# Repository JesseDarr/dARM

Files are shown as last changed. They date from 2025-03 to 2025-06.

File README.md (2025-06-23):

# dARM (dynamic Arm for Robotic Mischief)
dARM is a 3d printed 6 DOF robotic arm. Initially, I wanted to build a 3d printed arm as a test of my new `Bambu X1C`. I found most existing projects used stepper motors.  I wanted a better power density.

https://github.com/user-attachments/assets/527a8380-1c22-4416-9524-2030928b34a5

So the dARM journey began. The goal was to design a cheap, powerful, robust, modular, and easily maintained arm from scratch using `ODrive S1` BLDC controllers.  It stands `.975 meters` tall and can easily hold `5 lbs` in the horizontal position.

https://github.com/user-attachments/assets/cb6a208b-52ac-4bd4-9993-00c22c082488

After iterating through various designs, modularity and maintenance became top priorities.  If any individual component fails, its modular section can be removed from the larger arm for easy replacement.

## Table of Contents
1. [Versions](#versions)
2. [Inspirations](#inspirations)
   - [James Burton](#james-burton)
   - [Skyentific](#skyentific)
   - [OpenQDD](#openqdd)
   - [SSG48 Gripper](#ssg48-gripper)
   - [Gary McLendon](#gary-mclendon)
3. [Control](#control)
   - [Pi](#pi)
     - [Enable CAN Communication](#enable-can-communication)
     - [CAN Service](#can-service)
     - [Clone git repo](#clone-git-repo)
     - [Game Controllers](#game-controllers)
   - [CAN Wiring](#can-wiring)
4. [Power](#power)
   - [Power Box](#power-box)
   - [Power Wiring](#power-wiring)
5. [Mechanical](#mechanical)
   - [Primary Actuators](#primary-actuators)
   - [Forearm](#forearm)
   - [Gripper](#gripper)
   - [Pillars](#pillars)
6. [Assembly](#assembly)
   - [Sanding](#sanding)
   - [Glue](#glue)
   - [Bottom Up](#bottom-up)
   - [Motor Plates](#motor-plates)
   - [Brake Resistors](#brake-resistors)
7. [Links](#links)

## Versions
Version numbers are determined purely by emotion. Don't ask what SDE stands for.

| Version | Date | Notes |
|--- | --- | --- |
| 0.35 SDE  | 12/28/2024 | 6 axis, 7 motor design |
| 0.45 SDE  | 1/17/2025 | Gripper v2 added |
| 0.55 SDE  | 1/28/2025 | Power box added |
| 0.56 SDE  | 3/15/2025 | New gripper motor magnet holder | 
| 0.59 SDE  | 3/24/2025 | Dock and finger v4 added |
| 0.60 SDE  | 4/5/2025 | Gripper gear/magenet holder integration | 
| 0.62 SDE  | 5/2/2025 | ROS2 pkg: published in submodule | 
| 0.70 SDE  | 6/22/2025 | ROS2 pkg: teleop node and refined URDF  | 

## Inspirations
Without the below projects and youtube channels the dARM project wouldn't exist.  I can't thank them enough for the inspiration and advice they've provided.

#### [James Burton](https://www.youtube.com/@jamesbruton)
What can I say about James.  I've been watching his channel for years.  Initially, because he did interesting things with 3d printed parts, but shortly after that because the things he did were so consistently interesting.  James introduced me to ODrives as a control mechansim for BLDC motors.

#### [Skyentific](https://www.youtube.com/@Skyentific)
Another great youtuber.  He focuses on robotic arms, mostly 3d printed robotic arms. He covers specifics of design, assembly, and control for several different robot arms.  He also covers ODrives in great detail, including a video that uses a custom modified firmware to increase communication speed for specific queries over CAN.

#### [OpenQDD](https://www.aaedmusa.com/projects/openqdd)
The basis for the primary actuators are the OpenQDD by Aaed Musa.  Aaed also has an excellent [youtube channel](https://www.youtube.com/@aaedmusa). We use the same basic layout of an `8308 motor`, an `ODrive S1`, and a `planetary gearbox`. Our actuators have been redesigned from scatch to increase strength and rigidity, tighten tolerances, print easier, and to have more robust mounting capabilities.

#### [SSG48 Gripper](https://source-robotics.github.io/SSG48-gripper-docs/page1_about_the_gripper)
The basis for the gripper is the SSG48 project.  We use a different motor, controller, and mounting dimensions, but we keep the basic motor housing layout, MGN7C rail/carriers, and a rack and pinion to move the fingers.

#### Gary McLendon
Gary is an excellent electrical engineer, former owner of `GCM Computers`, and my former boss.  I want to thank Gary for the learning environment he provided me for nearly a decade under his employee.  I also want to thank him for the advice on the power system for the dARM.

## Control
The dARM is controlled with a `Raspberry Pi 4b` communicating to eight `ODrive S1s` via `CAN bus`.  This is achieved with the help of an `RS485 CAN Hat` on the Pi.  The ODrives are using the built in encoder with `encoder magnets` attached to each motor.

In a CAN network, the controller does not require a node ID, but each device on the network must have one. From this point forward, assume that the term "node" refers specifically to an ODrive and that node IDs are zero-indexed.

### Pi
The Pi is currently running `Ubuntu 22.04 Server`, but everything should still work with newer versions.  Instructions for installing Ubuntu on a Pi can be found [here](https://ubuntu.com/tutorials/how-to-install-ubuntu-on-your-raspberry-pi#1-overview).  Set the hostname to `pidarm` and the username to `darm`.  It is also recommened to set a `static IP address` so it can be easily accessed via SSH.

#### Enable CAN Communication
The CAN Hat communicates to our ODrives, but it must also communicate to the Pi.  This is done through a `Serial Peripheral Interface (SPI)`. To enable the interface edit `/boot/firmware/config.txt` and add the following at the bottom of the file:
```
dtparam=spi=on 
dtoverlay=mcp2515-can0,oscillator=12000000,interrupt=25 
dtoverlay=spi0-hw-cs
```
Reboot and run `dmesg | grep MCP2515` to verify the CAN Hat is now recognized.

Next we need to bring up the CAN interface with the following:
```
sudo ip link set can0 up type can bitrate 1000000
```
Then run `ip a` to veryify the interface is up.

Finally, install some handy CAN troubleshooting tools:
```
sudo apt-get install can-utils  <---- includes candump which can be used to see heartbeats from ODrives
sudo apt install python3-can    <---- includes CAN viewer script which can view all CAN traffic
```

#### CAN Service
A `systemd` service can be used to bring up the CAN interface on boot.  Create file `/etc/systemd/system/can0-setup.service` with the following contents:
```
[Unit]
Description=Set up CAN0 interface
After=network.target

[Service]
Type=oneshot
ExecStart=/sbin/ip link set can0 up type can bitrate 1000000

[Install]
WantedBy=multi-user.target
```

Then run the following commands:
```
sudo systemctl enable can0-setup.service
sudo systemctl start can0-setup.service
sudo systemctl status can0-setup.service
sudo reboot
```

Finally, run `ip a` to verify the CAN interface started on boot.

#### Clone git repo
`cd` to an appropriate directory and run `git clone https://github.com/JesseDarr/dARM.git` to clone the repo.  You will find the test scripts in the `odrive_tools` folder.  
> :bulb: **Note:**
> This folder is actually a git sub module that links to this repo: `https://github.com/JesseDarr/dARM_odrive_tools.git` 

#### Game Controllers
If you want to buy a cheap bluetooth dongle you can use an XBox One, XBox Series X, PS4 or PS5 controller with the `gamecontroller.py` script to control the dARM.  You will need to install the appropriate drives and use the `bluetoothctl` command to pair/connect the controller.  Run `ls /dev/input` and check for `js0` to ensure the controller is ready to work with the script.

Bluetooth on Linux is sketchy...bluetooth is sketchy...to combat this `reset_interfaces.sh` will reset the CAN and Bluetooth interfaces.  It can save a few reboots from time to time.

If using a Playstation Controller you also want to ensure the Sony module loads on boot.  Edit `/etc/modules` and add `hid-sony` to the bottom line.

### CAN Wiring
CAN wiring starts from the CAN Hat on the Pi.  A single `twisted pair` cable connects it to ODrive 0, which is then connected to ODrive 1, and so on with each ODrive daisy chained from the last like this:
```mermaid
graph LR
    subgraph "Raspberry Pi 4b"
        CAN_Hat[CAN Hat]
    end
    CAN_Hat <--> ODrive0[ODrive 0]
    ODrive0 <--> ODrive1[ODrive 1]
    ODrive1 <--> ODrive27[ODrive 2-7]
```

It's not well documented, but the ODrive S1 includes two `4-pin JST-GH` ports.  Each ODrive has 1 cable connected to the previous node and 1 cable connected to the next node.  It does not matter which port is used for which cable.  This allows some freedom when building custom length CAN cables.

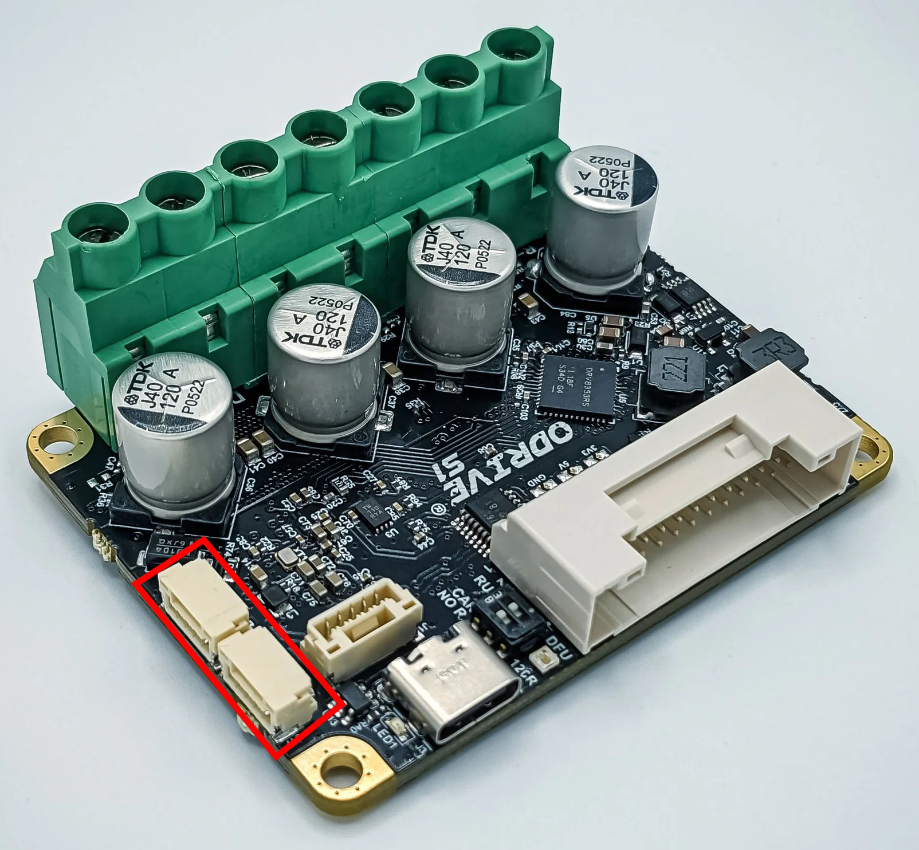
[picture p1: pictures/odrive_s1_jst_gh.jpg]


Be sure to enabled the `120ohm resistor on ODrive 7` by flipping the `DIP Switch` to `120R`.  All other ODrives should have this DIP Switch set to `No R`. 

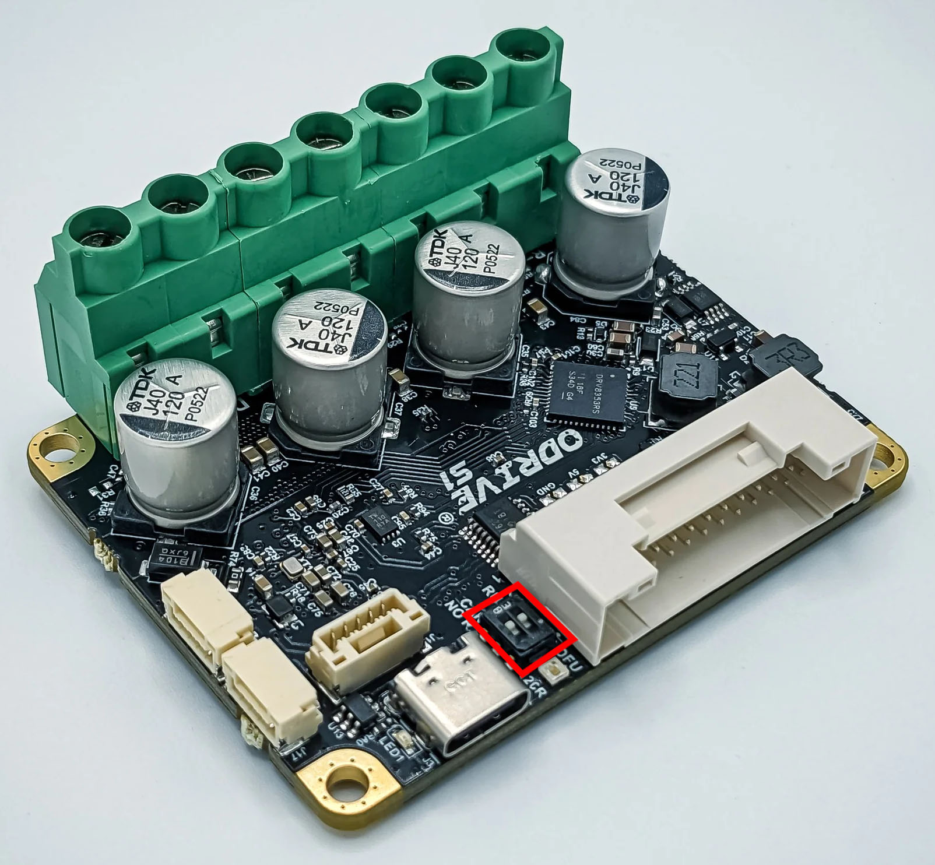
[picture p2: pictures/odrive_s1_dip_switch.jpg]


The BOM lists sacrifical 4pin JST-GH wires.  You will need to cut them in half and solder them into twisted pair.  You need to wire the twisted pair in a `roll over` fashion such that `PIN 2 is wired to PIN 2`, and `PIN 3 is wired to PIN 3`.  It is recommend to  solder 1 end connector onto the tiwsted pair, attach it to an ODrive, and then measure the required length of that cable.

The cable that connects the PI to ODrive 0 is a special case: it must also include `PIN 4` for ground.  It should be wired into the `CAN Hat` like this:

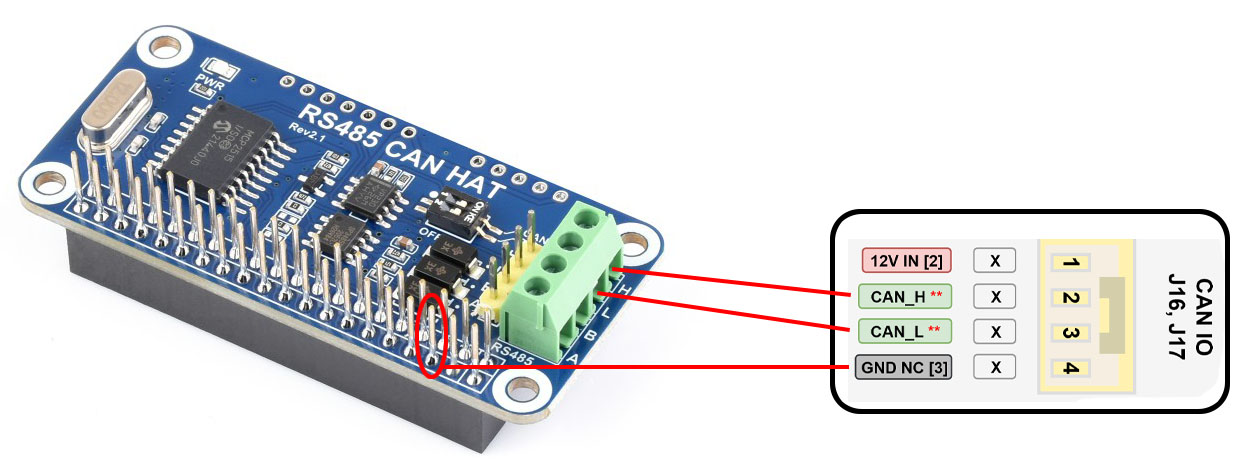
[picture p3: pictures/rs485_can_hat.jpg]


## Power
Power is provided by a `1200W 48V switching power supply`.  While this voltage exceeds the motors’ nominal ratings, each motor typically draws only 2–3 amps and operates intermittently rather than under continuous load.

### Power Box
The `switching power supply` along with a `power monitor` and `power switch` are packaged up inside our `power box`.  AC power goes in one side and DC power comes out the other.

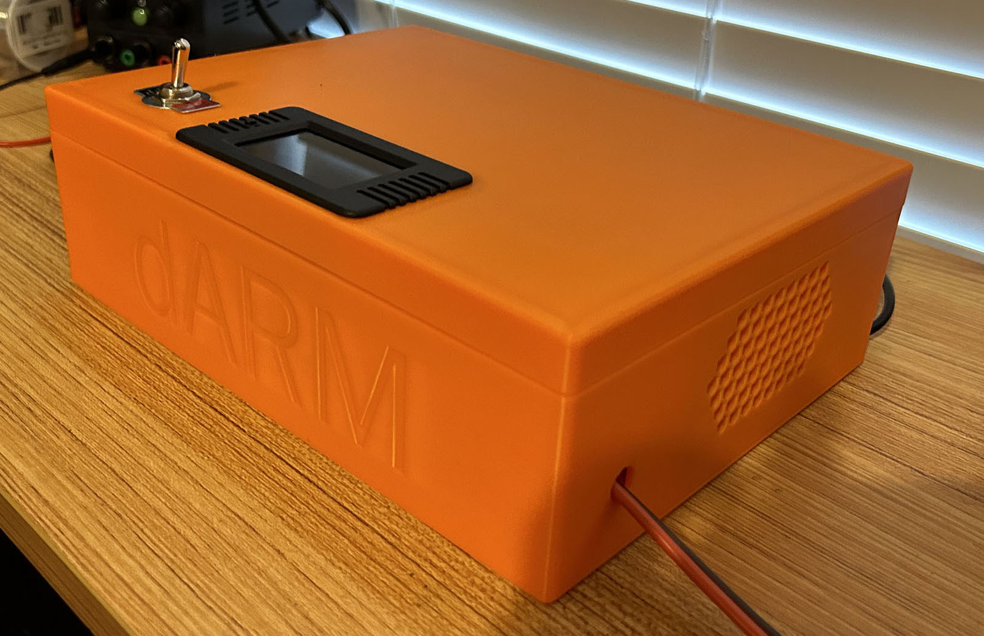
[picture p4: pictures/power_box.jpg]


The inside looks like this:

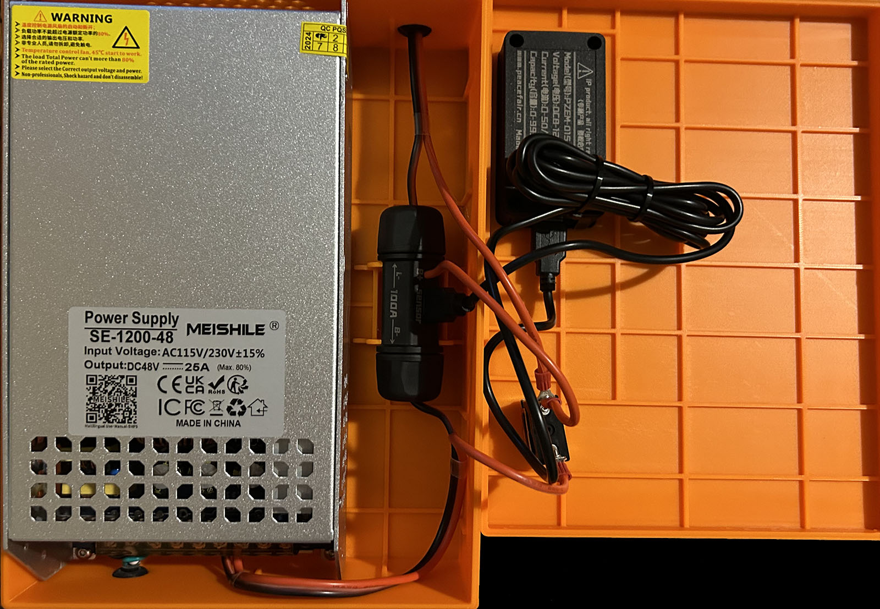
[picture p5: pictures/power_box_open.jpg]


Wiring diagram:

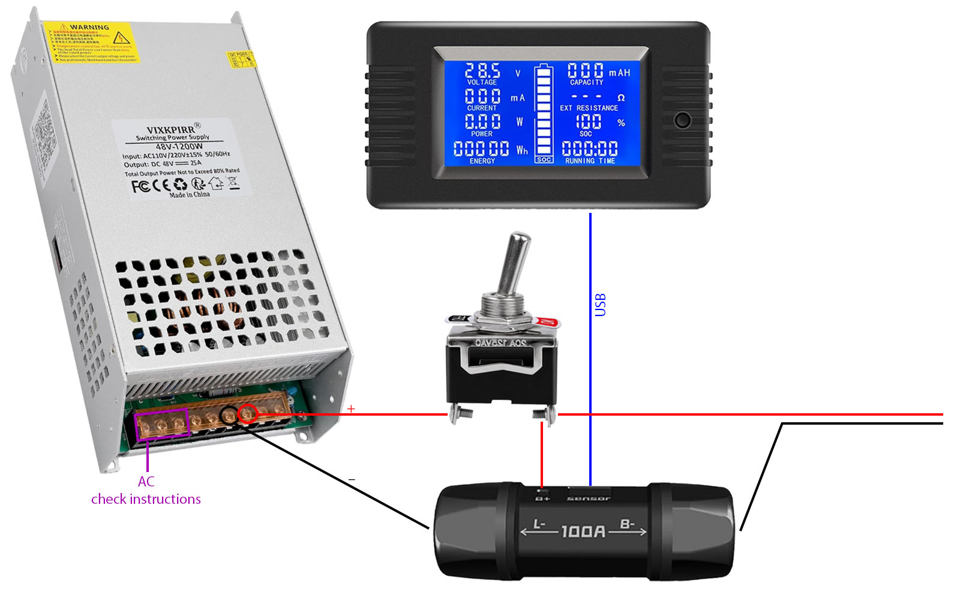
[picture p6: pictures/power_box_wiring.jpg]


### Power Wiring
Power wiring is all 14 AWG except for the gripper motor which is powerd with 18 AWG.  It is likely that the forearm motors could also be powered with 18 AWG.

Wiring a robot arm is difficult.  Wiring is all custom length and is measured after the robot has been assembled.  This allows a wire to be screwed into an ODrive, the respective joint moved to its most distant position, and an appropriate length of cable cut.

Wiring is also facilitated by `T Tap Connectors`.  These provide a T split at 90° and makes wiring much easier.  You can find them in the BOM.  Zip tie 2 of them bottom to bottom to handle both the positive and negative wires.  

Here is an overall power wiring diagram. 
```mermaid
%%{ init: { "flowchart": { "defaultRenderer": "elk" } } }%%
graph TD
    PowerBox[Power Box] --> XT90[XT90]
    XT90 --> T0( )
    XT90 --> ODrive0[ODrive 0]
    T0 --> T1( )
    T0 --> T2( )
    T1 --> ODrive1[ODrive 1]
    T1 --> ODrive2[ODrive 2]
    T2 --> ODrive3[ODrive 3]
    T2 --> T3( )
    T3 --> ODrive4[ODrive 4]
    T3 --> ODrive5[ODrive 5]
    ODrive5 --> ODrive6[ODrive 6]
    ODrive6 --> ODrive7[ODrive 7]
```
> :bulb: **Note:**
> Each line in the diagram represents both postive and negative wires, and each empty square represents a `T Tap Connector`.

## Mechanical
The dARM sits on top of a base made of 6 legs each holding a 5lb weight to provide a solid base.  

Joints 0–3 provide a single axis of rotation each and are powered by the primary actuators. Joint 1 carries the highest load and uses a dual-motor setup to provide the necessary torque. 

The forearm uses two motors connected through a two-stage belt system to drive a differential, enabling two independent axes of rotation. 

The gripper uses a single motor to drive a pair of `Compliant TPU fingers`.

### Primary Actuators
These are the modular building blocks of joints 0-3. Each actuator use an `Eagle Power 8308` BLDC motor mated to a `9:1 planetary gearbox`. 

The gear box uses a `helical angle of 15°`, a `pressure angle of 15°`, and a `module of 1.4 mm`.  Here are the tooth counts:
| Gear | Count |
|---|----|
| Sun | 8  |
| Planet | 28 |
| Ring | 64 |

The `primary actuators` come in 2 flavors: `single bearing` and `double bearing`.  

Double bearing actuators handle load perpendicular to the rotation axis better. They are used in joints that rotates on the vertical axis. 

Single bearing actuators are used in joints that rotate on the horizontal axis. 
> :bulb: **Note:**
> Joint 1 uses 2 single bearing actuators for increased power. This also eliminates the need for a double bearing actuator.

Below is an explode animation of each flavor.  They should give you a good idea of the sub components involved and are also a good assembly reference.

https://github.com/user-attachments/assets/06c78a0a-1a54-4e00-952e-c247763e0280

https://github.com/user-attachments/assets/b43786ba-b51d-407c-8697-83d8e092f9be

### Forearm
The forearm uses two `GB36-2` BLDC motors connected through a pulley system to drive a differential.  

The pulley system consists of two-stages.  Each uses `20 tooth` and `72 tooth`pulleys connected via a `300 mm GT2 belt`.  This provides a ratio of `3.6:1` per stage and a final drive ratio of `12.96:1`

The motors oppose each other.  If they are driven in opposite directions then the differential will `bend` along the `X axis`.  If they are driven in the same direction then the differential will `twist` along the `Z axis`.  

Interestingly, this means both motors are in use for every movement the differential makes.  So the final drive ratio approaches a `potential maximum` of approximately `26:1`.

The differential uses `Zerol Bevel Gears` made with [Bevel Gear Maker](https://apps.autodesk.com/FUSION/en/Detail/Index?id=2427789559362467821&appLang=en&os=Win64).  They pinion and wheel gears each have `38 teeth` for a final ratio of `1:1`.  Other measurements needed to reproduce the gears:

| Parameter | Value  |
|---|---|
| Module | 1.6 mm | 
| Pressure Angle | 25° |
| Face Width | 14 mm  |
| Clearance Factor | 0.3 mm | 

Below is an explode animation for the forearm:

https://github.com/user-attachments/assets/69bd7a27-f76a-4634-a556-fa9e3ffe39f6

### Gripper
The gripper uses a `GM5208-24` BLDC motor to drive a `rack and pinion` to articulate the `Compliant TPU Fingers` which ride along a `MGN7C rail`.

The compliant nature of the fingers as well as the rubbery TPU allow the fingers to change shape as they come in contact with an object.  They form around the object to provide a better grip.  The gripping surface is printed with `fuzzy skin` to provide additional friction.

The rack and pinion system has the following parameters:

| Parameter | Value |
|---|---|
| Module | 1.4 mm  |
| Pressure Angle | 30° |
| Gear Teeth | 8 |
| Rack Teeth | 10 |
| Gear Height | 11.2 mm |
| Rack Heigh | 7.7 mm  |

Below is an explode animation of the gripper:

https://github.com/user-attachments/assets/7afa1675-455d-4928-a6e3-7bdbb0bead69

### Pillars
Pillars are everywhere.  They are used to connect the legs to joint 0, they are used in all 5 of the primary actuators, and they are used again in the gripper.

They provide open space around the motors for improved air flow. A pair of them can be replaced with an adapter to provide sturdy connection point to other parts of the robot.

The strength of the pillars is a function of their cross sectional area.  This is used to our advantage by offsetting the bolt holes in the pillars in the primary actuators.  This allows for the total actuator diameter to be reduced by a few milimeters.

## Assembly
This section is a collection of tips for assembling the robot.

### Sanding
Some sanding is required, specifically anywhere a bearing will touch a printed part.  All bearings should be difficult to press fit into its coresponding part, but not too difficult as to deform the geometry of the part.  To achieve this type of fit sanding with `150 grit` sand paper is necessary.  Be paitent.  Sand, test fit, sand, test fit, sand, test fit, over and over.

Additionally if there are any blemishes on the mating surface of 2 printed parts they should be sanded flat.

### Glue
`CA glue`, otherwise known as `Super glue`, works wonders with PLA.  There is a nice little write up of the subject [here](https://www.instructables.com/Testing-the-Best-Glue-for-PLA-3D-Printed-Parts/).

It is recommended to glue in all nuts that are slotted in.  Not only does it ensure they won't fall out during assembly or maintenance, it also makes it much more difficult for a nut to "strip" the surounding PLA.

### Bottom Up
The modular units of the dARM should each be fully assembled first.  These units are:
 - Legs
 - Joint 0
 - Joint 1
 - Joint 2
 - Joint 3
 - Forearm
 - Gripper

Once these units are assembled piece them together from the bottom up.  It is recommended to pause building and to test all joints after each new joint is added to the robot.  `console.py` is perfect for this as it will dynamically add additional control sliders to the interface as additional ODrives are added to the network.

The `single bearing primary actuators` should be assembled in this order:
- Mount the `motor` to the `motor plate` (don't forget the magenet holder)
- Attach the `sun gear` to the `motor`
- Insert the `large bearing` into the `bearing holder`
- Build the `carrier base` around the `large bearing`
- Attach the `bearing holder` to the `motor plate` via the `pillars`
- Place the `ring gear` on top of the `bearing holder`
- Insert the `planet gears` onto the posts of the `bearing holder`
- Attach the `cover plate` and bolt the entire assembly together
- Attach the `carrier top` or `carrier adapter` depending on the joint

The `double bearing primary actuators` are the same as above save the additional step of placing the second `bearing holder` on top of the `ring gear` before attaching the `cover plate`.

### Motor Plates
There are several different motor plates.  They look mostly identical, but they are not.  There are small 1mm tall arcs used to guide our pillars into place since they have an offset bolt hole in them.  These arcs differ from actuator to actuator depending on a few factors.

The dARM.3mf file has the different motor plates clearly labeled.  Be sure to keep track of them or it will come at the price of disassembly/reassembly.

### Brake Resistors
Although they are not seen in any fo the CAD, all 5 primary actuators uses a `2 ohm brake resistor`.  Wiring instructions can be found on in the ODrive documentation.  Zip tie them to the standoffs holding the ODrive on the respective actuator.

## Links
Below is a list of useful links:

- [Ubuntu on PI](https://roboticsbackend.com/install-ubuntu-on-raspberry-pi-without-monitor/)
- [ODrive Configuration UI](https://gui.odriverobotics.com/configuration)
- [ODrive Documentation](https://docs.odriverobotics.com/v/latest/guides/getting-started.html)
- [ODrive Motor Tuning](https://docs.odriverobotics.com/v/latest/guides/tuning.html#tuning)
- [Planetary Gear Calculator](https://planetarygenerator.mateuszdrwal.com/)
- [Rack and Pinion Calculator](https://www.otvinta.com/rack.html)

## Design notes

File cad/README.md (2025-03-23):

# Step Files
These files allow anyone to easily modify and improve the dARM physical design in almost any CAD software.

## dARM.zip
This is the entire robot arm.  It is zipped because the .step file was larger than the 100 MB github limit.

Contains:
+ Legs
+ 5 Large Actuators
+ Forearm
+ Gripper
+ All subcomponents

## dock.step
TPU dock that tightly fits the base and 3rd joint in the resting position.
+ Acts as zero position
+ Make `endstop switches` unnecessary
+ Acts as cusion for the 3rd joint during shutdown sequence

## fingers.step
Additional compliant finger designs. Each plate is labeled by version starting with v4.  v3 is included in dARM.step.

## powerBox.step
Housing for switching power supply, power monitor, display, and on/off switch.
+ Early version
    - lid just seats on box
    - relies on its own weight

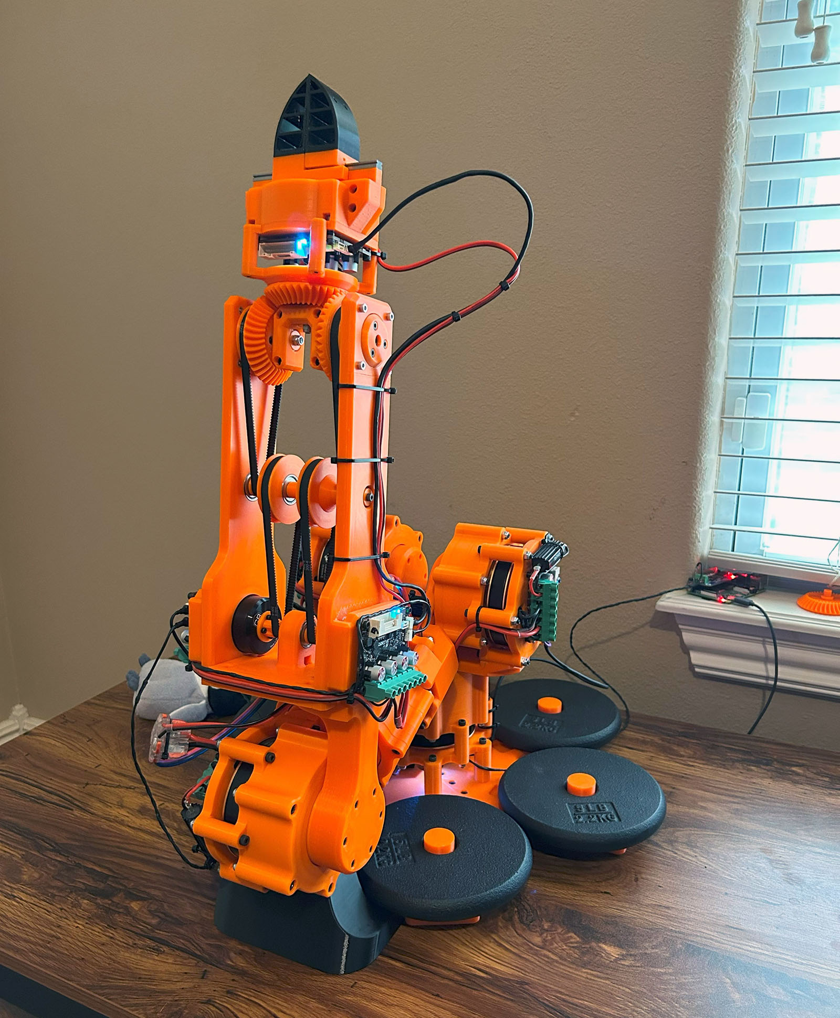
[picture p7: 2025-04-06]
pictures/corner.jpg

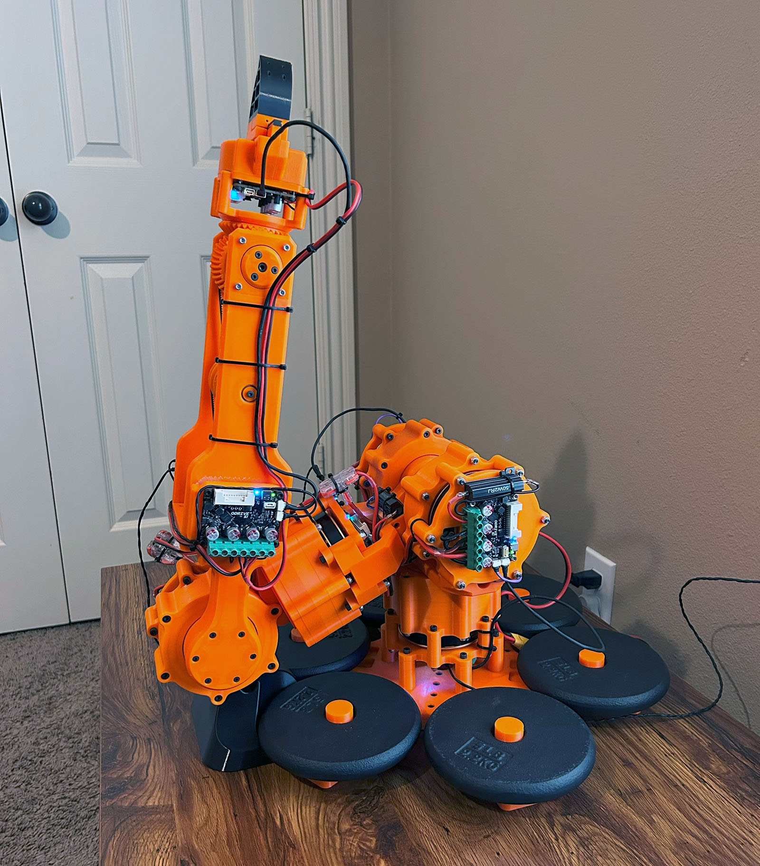
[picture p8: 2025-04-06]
pictures/side.jpg

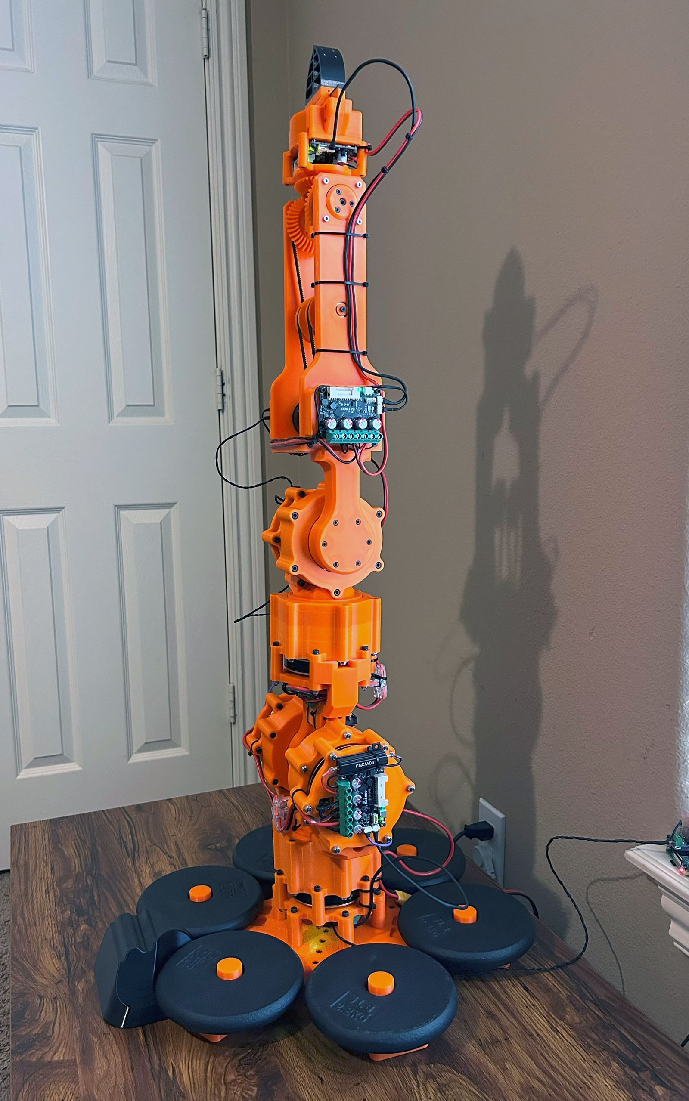
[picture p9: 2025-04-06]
pictures/side_tall.jpg

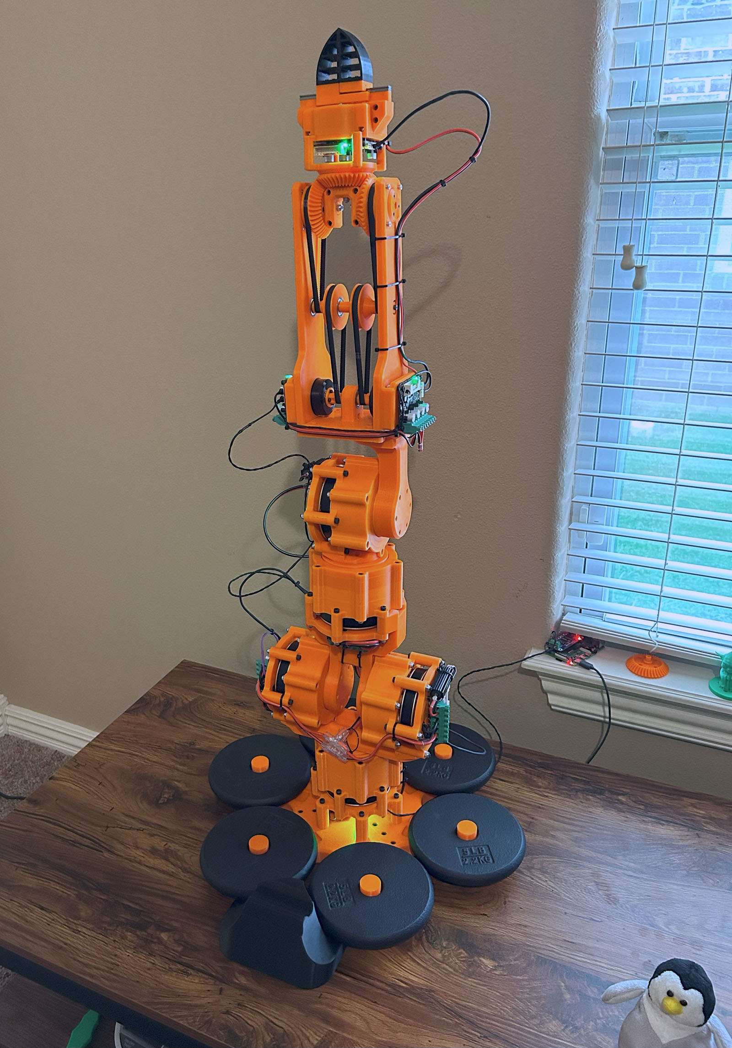
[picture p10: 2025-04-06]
pictures/corner_tall.jpg

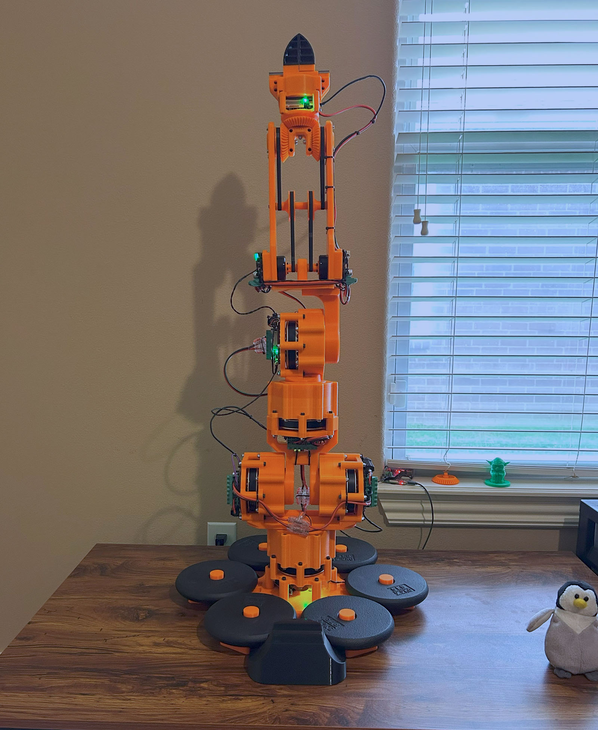
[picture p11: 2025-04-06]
pictures/front_tall.jpg

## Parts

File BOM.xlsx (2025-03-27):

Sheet: BOM
Item | Item Price | Count | Total Price
Power
48V 25A 1200W Switching Power Supply (https://www.amazon.com/Version-Converter-Switching-Transformer-Adapter/dp/B0CZLB573Z) | $69.99 | 1 | $69.99
Power Monitor (https://www.amazon.com/dp/B0CZ36J9BY) | $13.88 | 1 | $13.88
Power Switch (https://www.amazon.com/Nilight-Rocker-Toggle-Switch-Waterproof/dp/B078KBC5VH) | $10.99 | 1 | $10.99
Rubber Grommets | $4.29 | 1 | $4.29
Wires Standard (14 AWG) (https://www.amazon.com/dp/B07FMTCHC1) | $21.88 | 1 | $21.88
Wires Forearm/Gripper (18 AWG) (https://www.amazon.com/dp/B07FMRDP87) | $13.88 | 1 | $13.88
Wire T Connectors (https://www.amazon.com/dp/B09T628BXJ) | $14.99 | 1 | $14.99
Motors
GM5208-24 (https://shop.iflight.com/ipower-motor-gm5208-24-brushless-gimbal-motor-pro1347) | $42.99 | 1 | $42.99
GB36-2 (https://www.aliexpress.us/item/1281133501.html) | $61.35 | 2 | $122.70
EaglePower 8308 90KV (https://www.aliexpress.us/item/3256807861814061.html) | $53.00 | 5 | $265.00
Controll
ODrives S1 (https://odriverobotics.com/shop/odrive-s1) | $149.00 | 8 | $1192.00
Encoder Magnets (5 Pack) (https://odriverobotics.com/shop/set-of-5-encoder-magnets) | $9.00 | 2 | $18.00
Raspberry Pi 4 Model B (https://www.adafruit.com/product/4564?src=raspberrypi) | $75.00 | 1 | $75.00
RS485 CAN HAT (https://www.amazon.com/dp/B07DQPYFYV) | $16.31 | 1 | $16.31
Sacrificial JST GH 4 Pin Wires (https://www.amazon.com/dp/B0C2ZQHZ9T) | $9.99 | 1 | $9.99
Twisted Pair (100 Ft) (https://www.amazon.com/Jameco-ValuePro-Stranded-Twisted-Hook-Up/dp/B0CT5SXZLM) | $17.44 | 1 | $17.44
Hardware
Weights (https://www.amazon.com/dp/B00IHM82VW) | $18.99 | 3 | $56.97
MGN7C Rail 100mm and Carrier Block (https://www.aliexpress.us/item/3256804722090559.html) | $8.45 | 1 | $8.45
MGN7C Carrier Block (https://www.aliexpress.us/item/3256804722090559.html) | $4.57 | 1 | $4.57
GT2 Belts (300mm) (https://www.amazon.com/dp/B0BZNST13Y) | $12.99 | 1 | $12.99
Bolts, Nuts, and Pulleys | na | na | $212.77 | see hardware sheet
 |  |  | $2188.77 | total price

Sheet: Hardware
 | M2 |  | M2.5 | M3 |  |  |  |  |  |  |  |  | M4 |  |  |  |  | Bearings
 | Nut | 8 | 5 | Nut | Standoff | 6 | 10 | 12 | 15 | 25 | 30 | 35 | Nut | 10 | 16 | 45 | 60 | 75x95x10 | 30x37x4 | 12x28x8 | 8x22x7
Legs |  |  |  |  |  |  |  |  |  |  |  |  | 17 |  | 11 |  | 6
Joint 0 |  |  |  | 13 | 4 |  |  | 8 | 6 |  |  |  | 12 | 4 |  | 6 | 6 | 2 |  | 3
Joint 1 |  |  |  | 61 | 8 |  |  | 16 | 20 | 3 |  | 21 | 24 | 8 |  | 24 |  | 2 |  | 6 | 3
Joint 2 |  |  |  | 13 | 4 |  |  | 8 | 6 |  |  |  | 12 | 4 |  | 6 | 6 | 2 |  | 3 | 0
Joint 3 |  |  |  | 19 | 4 |  |  | 4 | 6 |  |  | 6 | 12 | 4 |  | 12 |  | 1 |  | 3 | 2
Forearm |  |  | 8 | 32 | 8 |  | 16 |  | 12 |  | 14 |  | 12 |  | 10 | 2 |  |  | 2 |  | 9
Gripper | 4 | 12 |  | 12 | 4 | 8 |  |  | 12 |  | 4
totals | 16 |  | 8 | 150 | 32 | 8 | 16 | 36 | 62 | 3 | 18 | 27 | 89 | 20 | 21 | 50 | 18 | 7 | 2 | 15 | 14 | 612 | count total
link | B0B93G1H9L (https://www.amazon.com/dp/B0B93G1H9L?th=1) |  | B0CXQ4QTGT (https://www.amazon.com/dp/B0CXQ4QTGT) | 90576A102 (https://www.mcmaster.com/90576A102) | B07M7D9PRM (https://www.amazon.com/dp/B07M7D9PRM) | 91290A111 (https://www.mcmaster.com/91290A111) | 91290A115 (https://www.mcmaster.com/91290A115) | 91290A117 (https://www.mcmaster.com/91290A117) | 91290A572 (https://www.mcmaster.com/91290A572) | 91290A125 (https://www.mcmaster.com/91290A125) | 91290A130 (https://www.mcmaster.com/91290A130) | 91290A135 (https://www.mcmaster.com/91290A135) | 90576A103 (https://www.mcmaster.com/90576A103) | 91290A144 (https://www.mcmaster.com/91290A144) | 91290A154 (https://www.mcmaster.com/91290A154) | 91290A145 (https://www.mcmaster.com/91290A145) | 91290A188 (https://www.mcmaster.com/91290A188) | 6815-2RS (https://www.amazon.com/dp/B082PYRJ4V?th=1) | B082PS9PHD (https://www.amazon.com/dp/B082PS9PHD) | B01K1OUR84 (https://www.amazon.com/dp/B01K1OUR84) | B099DP2FN7 (https://www.amazon.com/dp/B099DP2FN7)
pack size | 660 |  | 705 | 100 | 10 | 100 | 100 | 100 | 50 | 100 | 50 | 50 | 100 | 100 | 100 | 50 | 25 | 1 | 2 | 10 | 10
packs needed | 1 |  | 1 | 2 | 4 | 1 | 1 | 1 | 2 | 1 | 1 | 1 | 1 | 1 | 1 | 1 | 1 | 7 | 1 | 2 | 2
price per pack | $9.99 |  | $9.99 | $4.65 | $6.79 | $11.32 | $12.92 | $10.88 | $10.00 | $17.37 | $13.16 | $12.91 | $5.57 | $11.27 | $12.91 | $14.30 | $13.72 | $15.79 | $8.49 | $9.99 | $7.99
total prices | $9.99 |  | $9.99 | $9.30 | $27.16 | $11.32 | $12.92 | $10.88 | $20.00 | $17.37 | $13.16 | $12.91 | $5.57 | $11.27 | $12.91 | $14.30 | $13.72 | $110.53 | $8.49 | $19.98 | $15.98 | $212.77 | final total
For many parts only a handful are actually needed but they are sold in very large pack sizes. I recommend attempting to source these somewhere else.

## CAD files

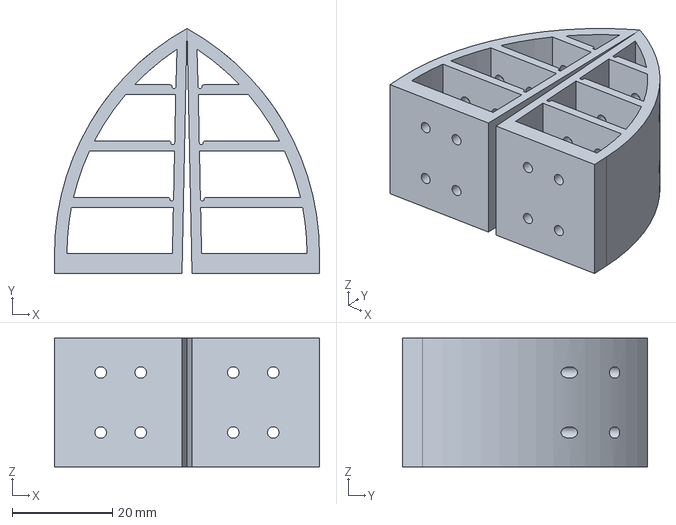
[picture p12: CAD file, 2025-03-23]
cad/fingers.step
53.0 x 49.0 x 25.7 mm

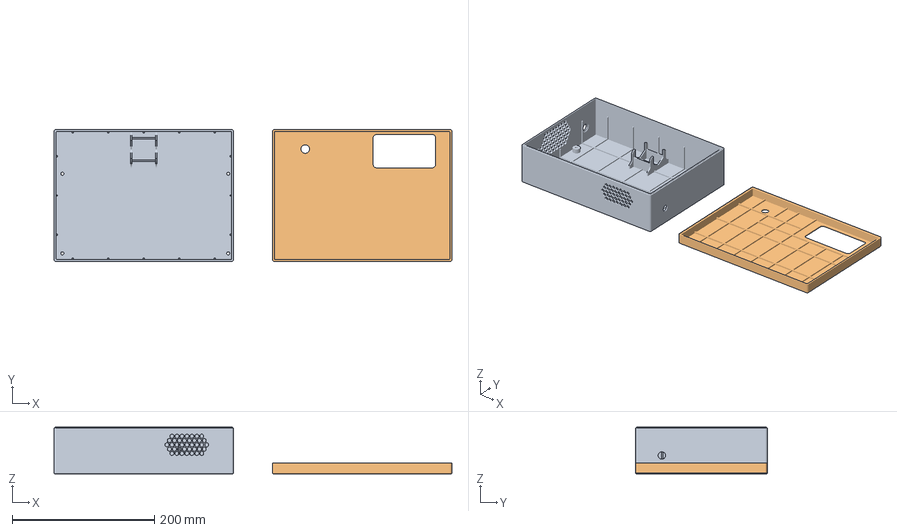
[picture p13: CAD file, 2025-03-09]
print/powerBox.3mf
560.2 x 185.8 x 66.0 mm
Base
Lid

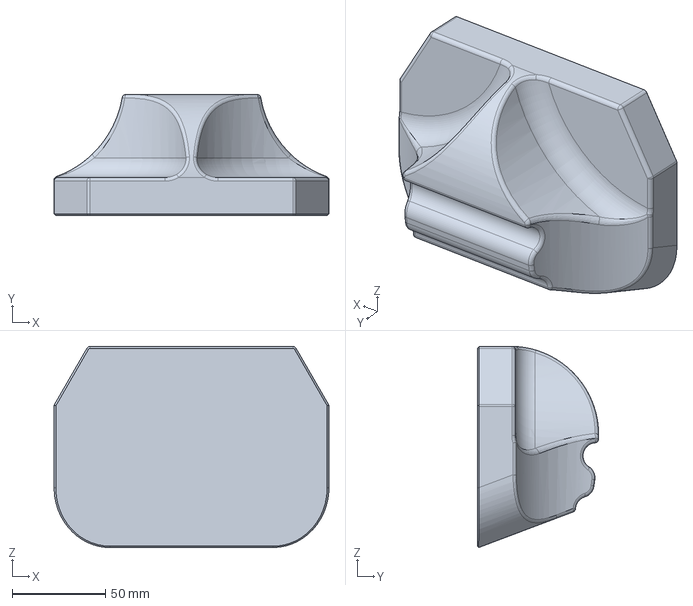
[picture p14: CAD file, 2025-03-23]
cad/dock.step
147.3 x 65.0 x 107.7 mm

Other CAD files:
print/dock.3mf
print/fingers.3mf

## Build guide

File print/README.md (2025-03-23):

# Print Files
This project was designed to be printed on 256 x 256 build plate.  

The print files were created for a Bambu X1C and others high speed, high quality consumer printers.

All settings, including build plate specific customizations, are in a pro
file named `dARM`.  
All plates should be printed in `PLA+`, except the gripper fingers and dock which should be `TPU`.

## dARM.3mf
This is the entire robot arm.
+ 36 Plates
+ Plate names are descriptive and include the print count

Contains:
+ Legs
+ 5 Large Actuators
+ Forearm
+ Gripper
+ All subcomponents

## dock.3mf
TPU dock that tightly fits the base and 3rd joint in the resting position.
+ Acts as zero position
+ Make `endstop switches` unnecessary
+ Acts as cusion for the 3rd joint during shutdown sequence

## fingers.3mf
Additional compliant finger designs. Each plate is labeled by version starting with v4.  v3 is included in dARM.3mf.

## powerBox.3mf
Housing for switching power supply, power monitor, display, and on/off switch.
+ Early version
    - lid just seats on box
    - relies on its own weight

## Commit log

2025-03-07 Added print_files with 3mf file and BOM.xlsx
    [BOM.xlsx]
2025-03-08 Updated .gitignore to exclude excel lock files, working on BOM data....counting screws
    [BOM.xlsx]
2025-03-08 Updated screw count through joint 3 and started working on the forearm
    [BOM.xlsx]
2025-03-08 Hardware section of BOM mostly completed, counting is done, need to double check all highlighted cells, measure finger screws, and collect pricing/links/identifier numbers
    [BOM.xlsx]
2025-03-08 Finished hardware count in BOM, still need to go track down links, identifier numbers and pricing
    [BOM.xlsx]
2025-03-08 Completed Hardware section of BOM with links and pricing included. Minor change to dARM.3mf file to add fuzzy skin to TPU finger
    [BOM.xlsx]
2025-03-08 Finished BOM, for now, total price $2,117.53 not including filament
    [BOM.xlsx]
2025-03-08 Added wire t connectors and weights to BOM
    [BOM.xlsx]
2025-03-08 Changed git modules file so we can automatically pull the main branch of the odrive tools repo
2025-03-09 Updated print file readme
2025-03-09 Added rubber grommets and power switch to BOM
    [BOM.xlsx]
2025-03-09 Added powerBox.3mf
2025-03-13 Updated dARM.3mf with refined magnet holder for the gripper motor
2025-03-14 added arm animation video
2025-03-14 updated arm video
2025-03-14 support modifiers for the gripper motor housing
2025-03-15 Changed folder names, added simulation folder which contains a URDF and it's associated STL files
    [base_link.stl, finger_1.stl, finger_2.stl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]
2025-03-15 Removed old files
    [base_link.stl, dARM.urdf, finger_1.stl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]
2025-03-15 Imported files from fusion2urdf-ros2 and updated readme file
    [Arm.xacro, base_link.stl, finger_1_1.stl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]
2025-03-18 Added RS485 CAN Hat to BOM
    [BOM.xlsx]
2025-03-19 Added odrive pictures
2025-03-19 testing image insert
2025-03-19 wrote some wiring stuff
2025-03-19 Almost finished wiring section, still needs picture of PI/Can Hat
2025-03-19 think I finished the CAN Wiring section
2025-03-22 Added fingers.3mf
2025-03-22 Updated readme and added dock.3mf
    [dock.3mf]
2025-03-22 Updated fingers and dock 3mf files
    [dock.3mf, fingers.3mf]
2025-03-23 dock and fingers step files and readme updates
    [dock.step, fingers.step]
2025-03-23 updated simulation files with dock
    [dock__1__1.stl]
2025-03-26 added pictures of power box and added them to readme, need to get this to main
2025-03-26 Updated BOM with correct power supply price and link
    [BOM.xlsx]
2025-03-27 Added power box wiring diagram
2025-04-05 Added new gripper sun gear/magnet holder redesign to dARM.3mf file
2025-04-05 Added new gripper sun gear/magnet holder redesign to dARM.zip in cad folder
2025-04-22 fixed base_link and replaced gripper and differential stl files, much smaller file sizes now
    [base_link.stl]
2025-04-29 simulation folder was removed, a ros2 package is currently being built in another repo and will soon be added as another sub module to this repo
    [Arm.xacro, base_link.stl, differential_1.stl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]
